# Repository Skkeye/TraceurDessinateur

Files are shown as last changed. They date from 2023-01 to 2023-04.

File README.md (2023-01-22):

# TraceurDessinateur
Projet Final Cegep

## Contexte/Origine
Le dessin est un art qui est difficile à apprendre et à maîtriser, alors l’option de prendre une photo pour décrire une scène devient très intéressante pour un artiste dépourvu de talent de dessinateur. Le TraceurDessinateur entre en jeu pour donner un compromis entre le dessin et la photo.

## Besoin General
Le besoin est de pouvoir dessiner un ou des objets sans pour autant avoir du talent pour dessiner. La partie cadrage et pinceau doivent être sans fil et rechargeable et doivent pouvoir être utilisés dans la majorité des environnements. La partie dessinateur doit être capable d'être configurable et facile à utiliser. 

## Objectif
L’objectif ici est de concevoir et de réaliser un pinceau 3d et une caméra de cadrage connectée par wifi au dessinateur qui lui pourra dessiner sur une feuille de papier.

## Fonctions Principales
La solution aura 3 parties principales en plus de la partie serveur qui connectera le tout. La première partie consiste d’une manette connectée au serveur par wifi, la deuxième d’une caméra qui détecte la position de la manette et la troisième d’un système de moteurs pas-à-pas pour dessiner sur une feuille de papier.
- La solution doit pouvoir voir et trouver la position de la manette via une caméra.
- La solution doit pouvoir choisir la couleur de la manette en fonction des couleurs perçus par la caméra.
- La solution doit pouvoir capter une force variable avec la manette.
- La solution doit consister d’une manette et d’une caméra portatives.
- La solution doit consister d’une manette et d’une caméra qui se connectent à un serveur WiFi dédié.
- La solution doit pouvoir dessiner à l'aide d’une machine CNC 2.5 axes.
- La solution doit être configurable via un menu contrôle avec un encodeur de rotation avec bouton.
- La solution doit avoir une caméra pour aider à positionner la caméra.
- La solution doit pouvoir être alimentée par une cellule LiPo pour la manette et la caméra.
- La solution doit avoir un bouton Marche/Arret sur le Dessinateur, la Caméra et la Manette.

## Contraintes
- Tension d’alimentation principale : 120 VAC
- Tension d’alimentation moteurs pas à pas : 4.1 VDC
- Tension d’alimentation de la caméra et la manette : 3.3v (LiPo 3.7v)
- Connexion sans fils : WiFi
- Application sur microcontrôleurs

## Livrables
- Produits Assembles : Manette, Camera, Dessinateur
- Logiciels installés sur les microcontrolleurs

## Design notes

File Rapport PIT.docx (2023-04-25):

Olivier David Laplante

Technique Systèmes Ordinés

Rapport du Projet d'Intégration en TSO TraceurDessinateur

Travail présenté à :

Francis Lance

Dans le cadre du cours

247-6E2-HU PIT

Groupe 201

Cégep de l’Outaouais

Campus Félix-Leclerc

Le 25 Avril 2023

# Table des matières

Table des matières 2

Introduction 3

But 3

Caractéristiques 3

Faisabilité 3

Dans le temps 3

Économiquement 3

Technologiquement 3

Diagrammes 5

Fonctionnel 5

Schématiques 6

Matriciel 8

Evaluation des coûts 9

Programmatique 10

Organigrammes 10

Manette 10

Serveur 11

Dessinateur 12

Pseudo-code 13

Manette 13

Serveur 14

Dessinateur 15

Code 16

Dessinateur.ino 16

StepperWrapper.h 22

StepperWrapper.cpp 26

Manette.ino 31

MQTTBroker.ino 38

Discussion 44

Problèmes et Solutions 44

Tests 44

Utilisations 44

Ameliorations 44

Reproduction 45

Matériel 45

Programmation 45

Environnement 45

Logiciels 45

Installer les pilotes 46

Procédé 46

Installer le logiciel du "Contrôleur USB" 46

Installer le logiciel du "Dessinateur" 46

Installer le logiciel de la "Manette" 46

Vérifications 46

Assemblage 47

Assurer le bon fonctionnement 47

Conclusion 48

Annexe A 49

Annexe B 50

Manuel de l’utilisateur 50

Consignes de sécurité 50

!Avertissements 50

!Attention 50

Attention 50

Table des matières 50

Caractéristiques 50

Définitions 50

Installation 51

Matérielle 51

Mise en marche 51

Mise en arrêt 51

Utilisation 51

Fonctionnement 51

Mode d'emploi 51

Dépannage 52

Section avancée 53

Prérequis 53

Accéder à la console de commandes 53

Les commandes 54

Réinstaller les logiciels 54

Installer les pilotes 54

Installer le logiciel du "Contrôleur USB" 54

Installer le logiciel du "Dessinateur" 55

Installer le logiciel de la "Manette" 55

Dépannage avancé 55

Annexe C 56

Manuel de dépannage 56

Problème 1 56

Tests 56

Hypothèses 56

Meilleurs Tests 56

Modifications 56

Vérification 56

Problème 2 56

Tests 56

Hypothèses 56

Meilleurs Tests 56

Modifications 56

Vérification 56

Problème 3 56

Tests 56

Hypothèses 56

Meilleurs Tests 56

Modifications 56

Vérification 56

# Introduction

## But

Le but était de concevoir et de réaliser un pinceau 3D connectée par wifi au dessinateur qui lui pourra dessiner sur une feuille de papier.

## Caractéristiques

## Faisabilité

### Dans le temps

Malgré que j'ai fini par manquer de temps pour achever le projet,

je le blâme purement sur la planification et sur les défis inutiles que je me suis placé pour rendre le projet plus intéressant. Si j'avais simplifié au lieu de complexifier et que mon échéancier était fondé sur mes capacités, je crois sincèrement que le temps n'aurait pas été un problème.

### Économiquement

À part la machine CNC qui m'a été prêté pour ce projet, toutes les autres composantes ne sont pas excessivement coûteuses (~100$ avec optimisations).

### Technologiquement

Les technologies utilisées dans ce projet sont très développées et accessibles pour tous. La composante la plus récente est le Raspberry Pi Pico W qui est sorti en juillet 2022.

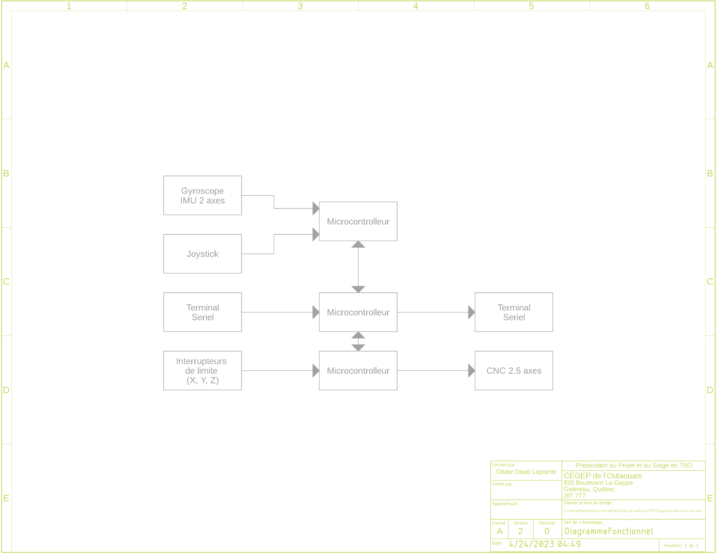
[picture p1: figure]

# Diagrammes

## Fonctionnel

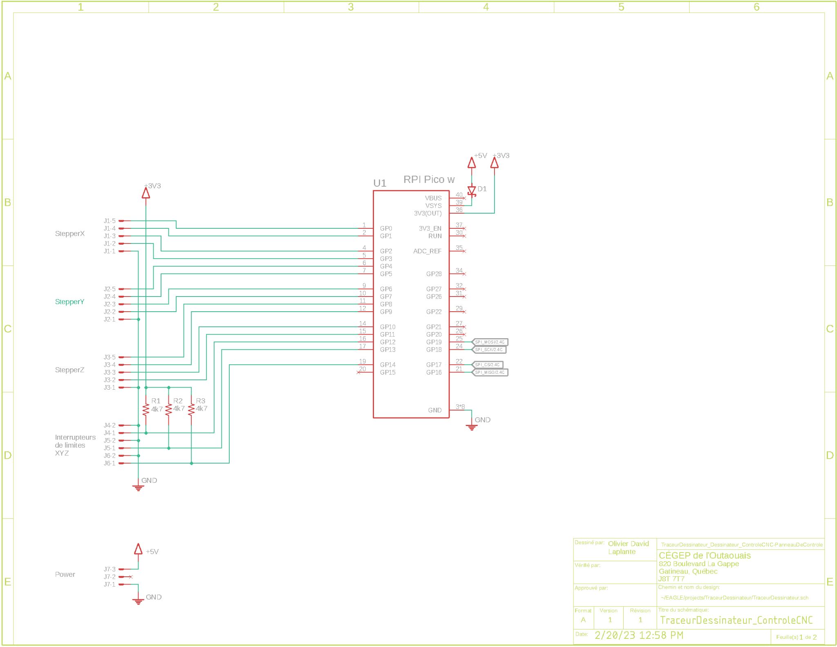
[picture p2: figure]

## Schématiques

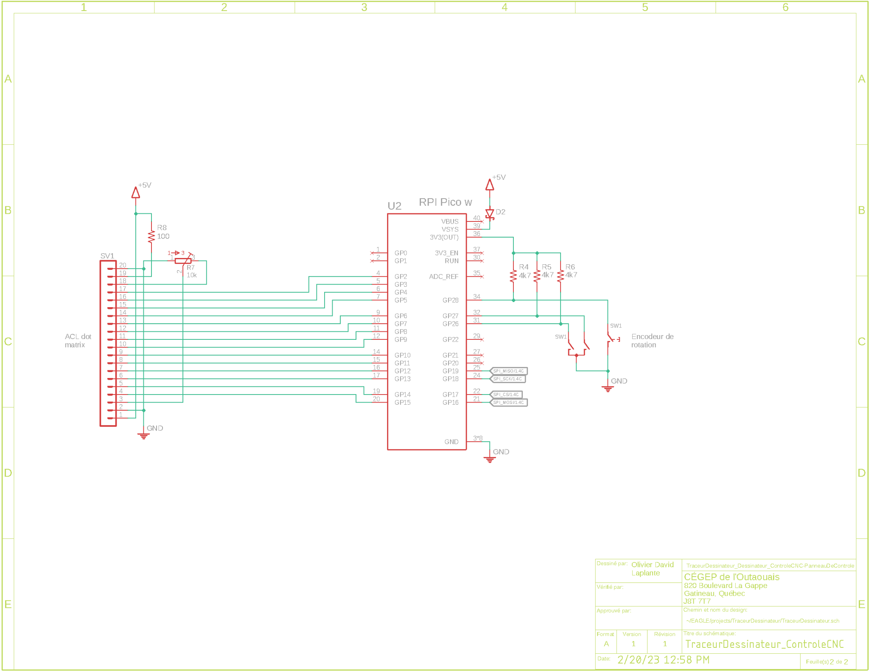
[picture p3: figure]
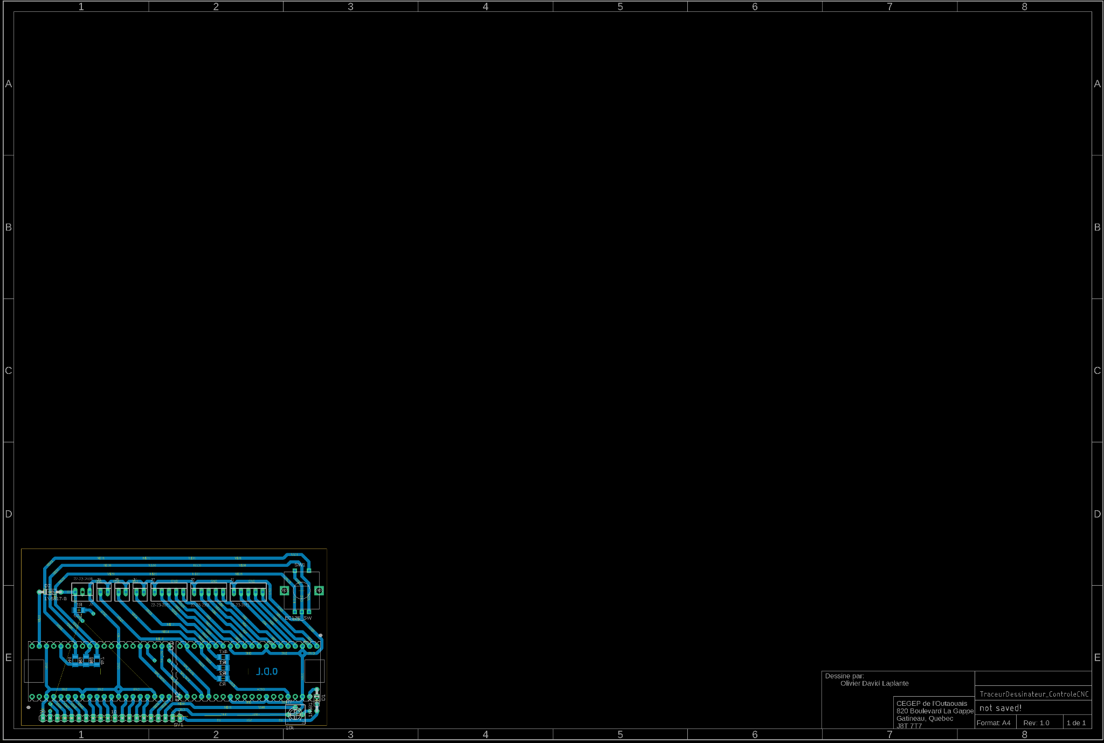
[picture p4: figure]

## Matriciel

## Evaluation des coûts

# Programmatique

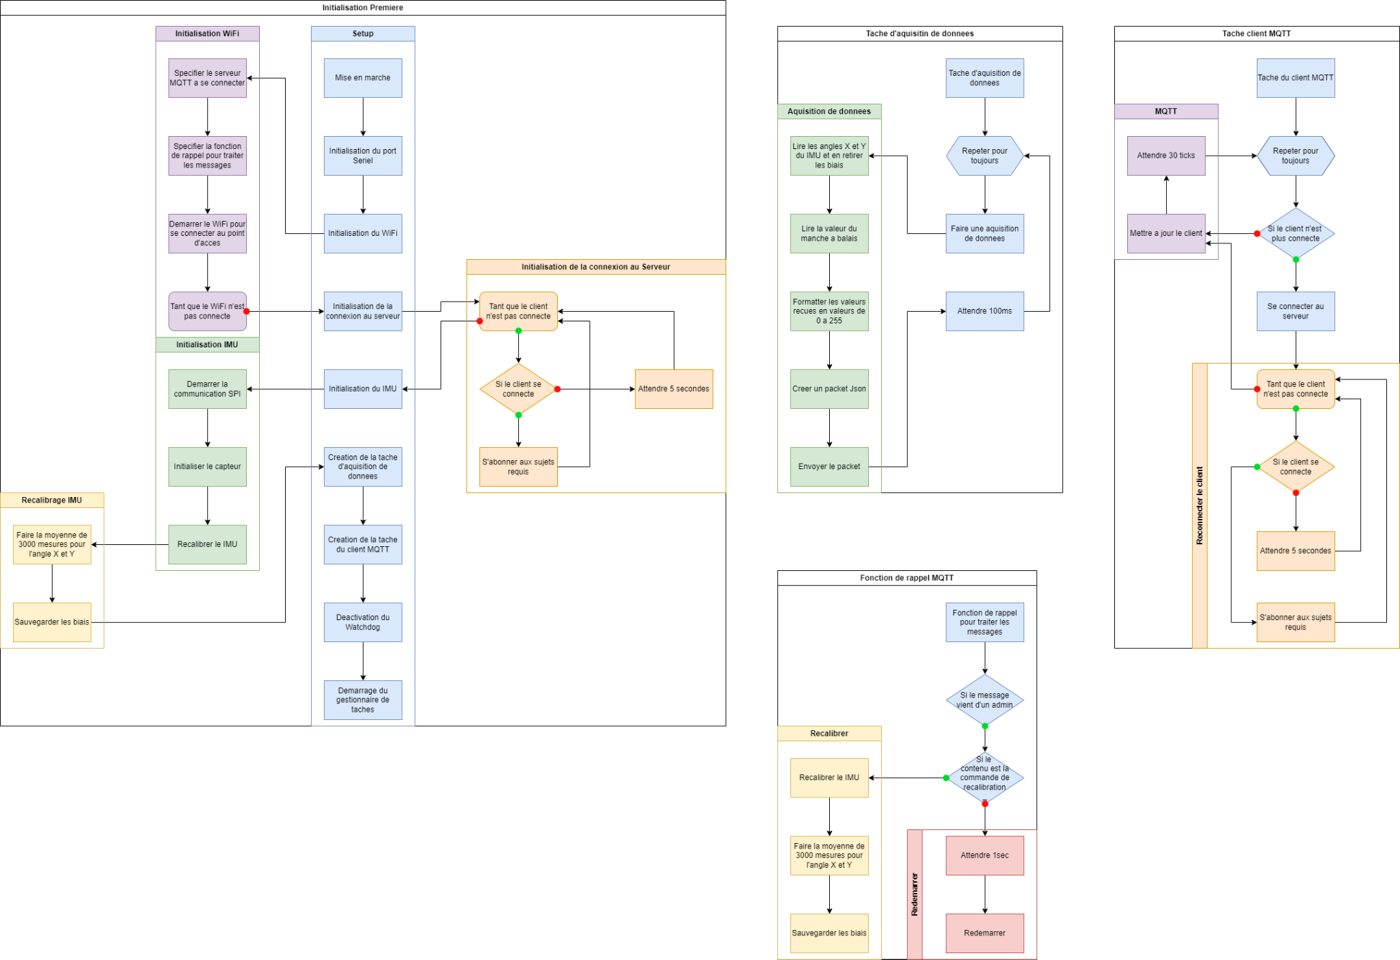
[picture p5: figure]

## Organigrammes

### Manette

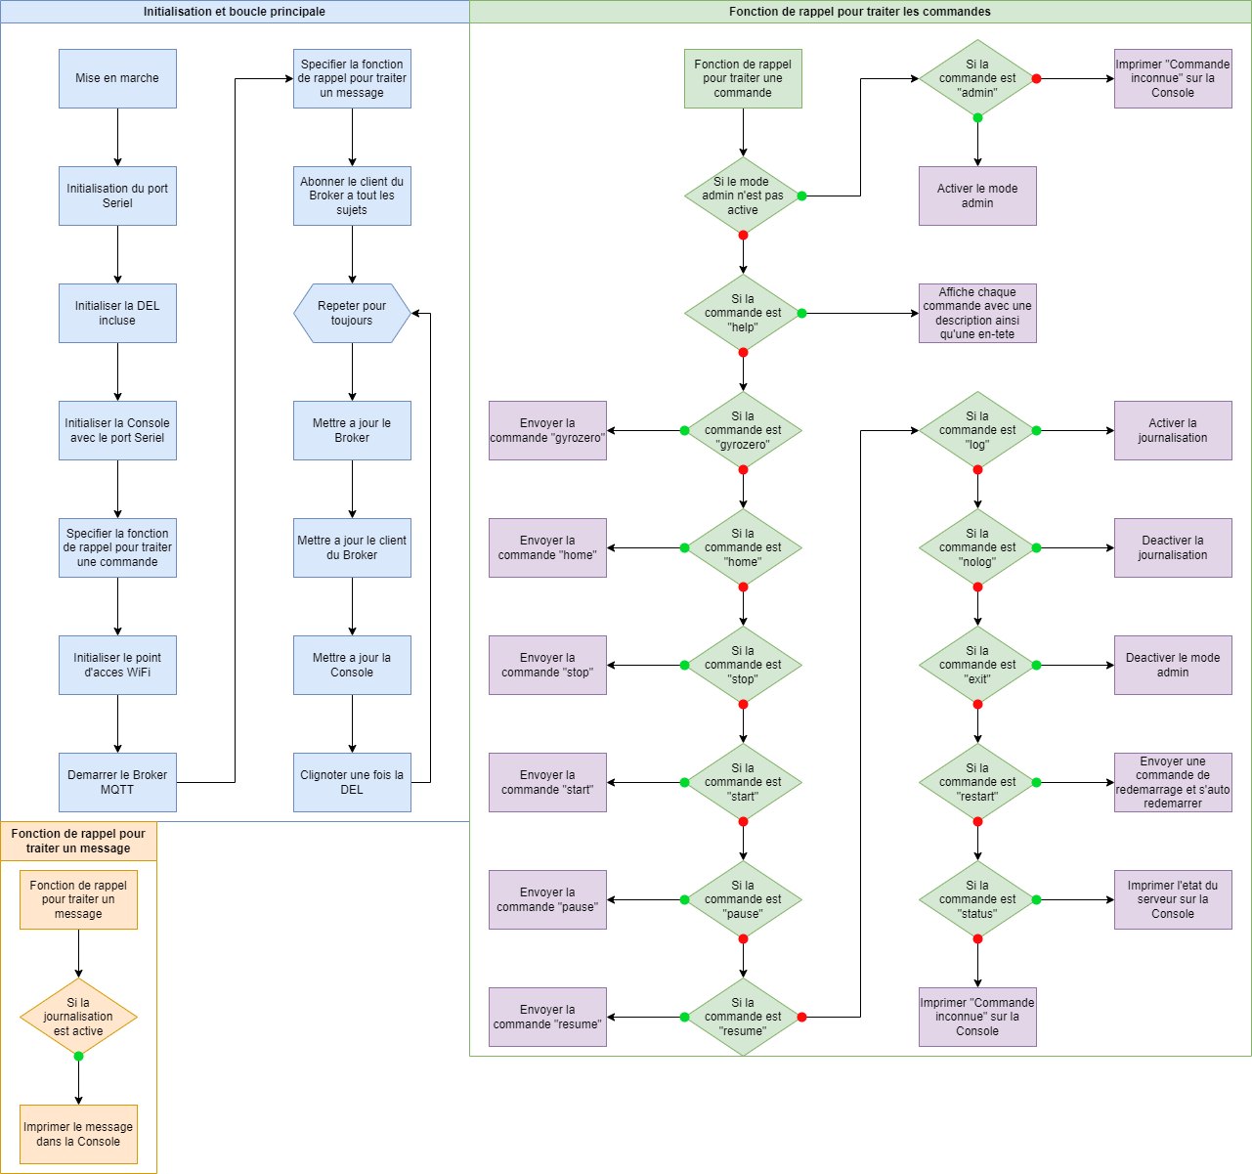
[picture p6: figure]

### Serveur

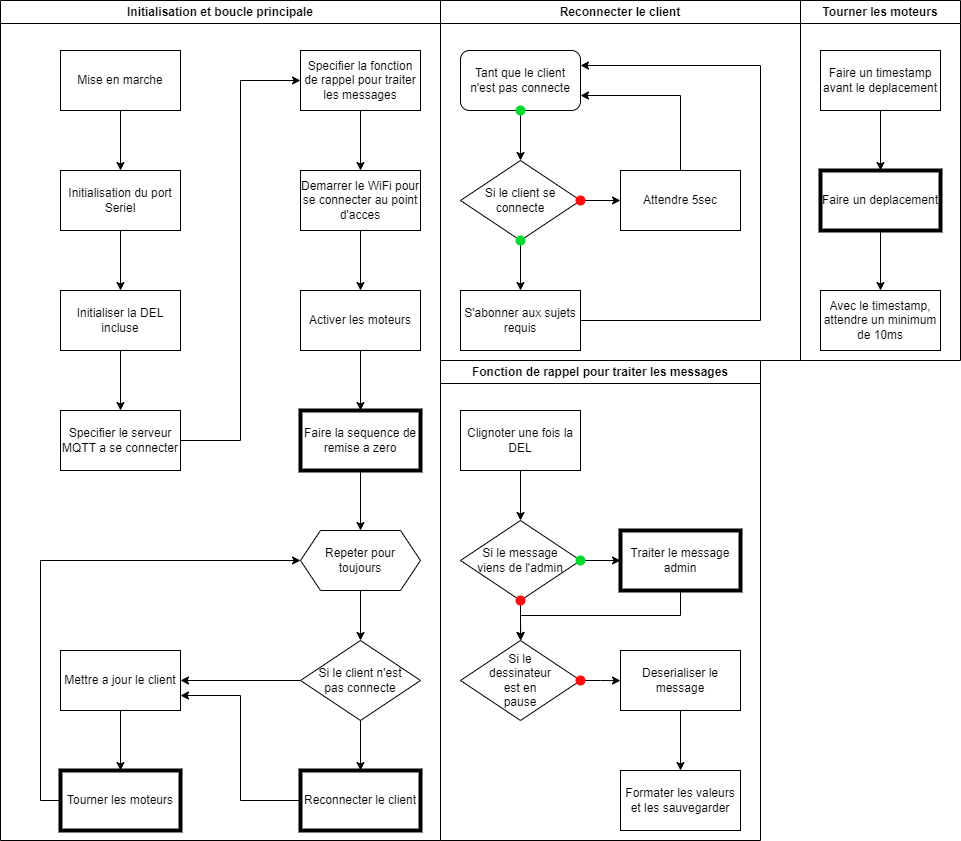
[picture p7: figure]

### Dessinateur

## Pseudo-code

### Manette

### Serveur

### Dessinateur

## Code

### Dessinateur.ino

/**

* @file AllInOneDessinateur.ino

* @brief Fichier principal du dessinateur

*

* Olivier David Laplante -- 8 Avril 2023 : Creation

*/

//#include <wiring_private.h>

#include "StepperWrapper.h"

#include <ArduinoJson.h>

#include <WiFi.h>

#include <PubSubClient.h>

// Definitions de constantes

#define NAME "Broker PIT"

#define PORT 1337

const IPAddress server_ip(192, 168, 144, 1);

// Variables et instances globales

DynamicJsonDocument doc(256);

char message[256] = "";

WiFiClient wifi_client;

PubSubClient client(wifi_client);

// Steppers

StepperWrapper stepper_x(0, 1, 2, 12, 12845 * 4);

StepperWrapper stepper_y(4, 5, 6, 13, 10752 * 4);

StepperWrapper stepper_z(8, 9, 10, 14, 1325 * 4, true);

ThreeAxisStepper steppers(&stepper_x, &stepper_y, &stepper_z);

bool paused = false;

// Variables pour les deltas

int deltaX = 0;

int deltaY = 0;

int deltaZ = 0;

/**

* @brief Fonction qui gère les messages admin

*

* @param topic : topic du message

* @param payload : payload du message

* @param lenght : longueur du payload

*/

void adminMessage(char *topic, uint8_t *payload, unsigned int lenght)

{

if (strcmp((char *)payload, "home") == 0) // home : mise a zero de la position

{

paused = true;

steppers.home();

paused = false;

}

else if (strcmp((char *)payload, "start") == 0) // start : demarrage des moteurs

{

steppers.enable();

}

else if (strcmp((char *)payload, "stop") == 0) // stop : arret des moteurs

{

steppers.disable();

}

else if (strcmp((char *)payload, "pause") == 0) // pause : pause les déplacements

{

paused = true;

}

else if (strcmp((char *)payload, "resume") == 0) // resume : reprend les deplacements

{

paused = false;

}

else if (strcmp((char *)payload, "restart") == 0) // restart : redémarre le RP2040

{

digitalWrite(LED_BUILTIN, HIGH);

delay(1000);

digitalWrite(LED_BUILTIN, LOW);

rp2040.reboot();

}

}

/**

* @brief Fonction qui fait clignoter la LED

*

*/

void vShortBlink()

{

digitalWrite(LED_BUILTIN, HIGH);

delay(1);

digitalWrite(LED_BUILTIN, LOW);

delay(1);

}

/**

* @brief Fonction qui gère les messages MQTT

*

* @param topic : topic du message

* @param payload : payload du message

* @param lenght : longueur du payload

*/

void callback(char *topic, uint8_t *payload, unsigned int lenght)

{

vShortBlink(); // blink led

// Si le message est un message admin

if (strcmp(topic, "admin") == 0)

{

adminMessage(topic, payload, lenght);

return;

}

if (paused) // Si le dessinateur est en pause on ne fait rien

{

return;

}

deserializeJson(doc, payload); // On désérialise le message

// On calcule les deltas

deltaY = (int)((short)doc["angle_x"] / 2) - 63;

deltaX = (int)((short)doc["angle_y"] / 2) - 63;

deltaZ = (int)((short)doc["bouton"] / 2) - 63;

client.flush();

}

/**

* @brief Fonction qui fait tourner les moteurs

*

*/

void runSteppers() {

unsigned long time = millis();

steppers.move(deltaX, deltaY, deltaZ);

delay((10 > (millis() - time)) ? (10 - (millis() - time)) : 0); // On attend jusqu'a 10ms pour avoir un delai constant

}

/**

* @brief Fonction qui reconnecte le client MQTT

*

*/

void reconnect()

{

// Boucle jusqu'à ce que le client se connecte

while (!client.connected())

{

Serial.print("Attempting MQTT connection...");

// essaye de se connecter

if (client.connect("arduinoClient"))

{

Serial.println("connected");

// Une fois connecté on s'abonne aux topics

client.subscribe("inTopic");

client.subscribe("admin");

}

else

{

Serial.print("failed, rc=");

Serial.print(client.state());

Serial.println(" try again in 5 seconds");

// On attend 5 secondes avant de recommencer

delay(5000);

}

}

}

/**

* @brief Fonction qui setup le dessinateur

*

*/

void setup()

{

Serial.begin(115200); // On initialise le port serie

pinMode(LED_BUILTIN, OUTPUT); // On initialise la LED builtin

// On initialise le client MQTT

client.setServer(server_ip, PORT);

client.setCallback(callback);

// On se connecte au WiFi

WiFi.mode(WIFI_STA);

WiFi.begin(NAME);

// on active les moteurs

steppers.enable();

// On met les moteurs a zero

steppers.home();

}

void loop()

{

if (!client.connected()) // Si le client n'est pas connecte on se reconnecte

{

reconnect();

}

client.loop(); // On fait tourner le client MQTT

runSteppers(); // On fait tourner les moteurs

}

### StepperWrapper.h

/**

* @file StepperWrapper.h

* @brief Les definitions pour manipuler des moteurs steppers

*

* Olivier David Laplante -- 8 Avril 2023 : Creation

*/

#pragma once

/**

* @class StepperWrapper

* @brief Objet pour simplifier un moteur stepper

*

*/

class StepperWrapper {

private:

int dir_pin, step_pin, en_pin, home_pin;

long max_distance_from_origin;

bool positive_direction;

bool direction;

/**

* @brief Initialise les pins relative au moteur

*/

void initPins();

public:

long distance_from_origin;

/**

* @brief Le constructeur pour le stepper

*

* @param dir La pin de direction

* @param step La pin de step

* @param en La pin enable

* @param home La pin de l'interrupteur de limite

* @param max_distance La distance maximale en pas

* @param flip_dir Change la direction par defaut (defaut = false)

*/

StepperWrapper(int dir, int step, int en, int home, int max_distance,

bool flip_dir = false);

/**

* @brief Fait un pas

*

* @param force Force le pas meme si on est a la limite

*/

void step(bool force);

/**

* @brief Change l'etat de la pin de direction

*

* @param dir La nouvelle direction

*/

void setDir(bool dir);

/**

* @brief Change l'etat de la pin enable

*

* @param en L'etat

*/

void setEnabled(bool en);

/**

* @brief Verifie si l'interrupteur est enfonce

*

* @return bool Si enfonce

*/

bool isHome();

};

/**

* @class ThreeAxisStepper

* @brief Manipule 3 moteurs stepper simultanement

*

*/

class ThreeAxisStepper {

private:

StepperWrapper *stepper_x, *stepper_y, *stepper_z;

/**

* @brief Utilise pour repartir egalement les pas des moteurs

*

* @param this_step Le nombre de pas que le moteur a fait durant ce

* deplacement

* @param count Le nombre de pas de ce deplacement

* @param steps_moving Le nombre de pas requis pour ce moteur pour ce

* deplacement

* @param largest_step_count Le plus grand nombre de pas requis pour de

* deplacement

* @return Si le moteur fait un pas

*/

bool doesStep(int this_step, int count, int steps_moving,

int largest_step_count);

public:

/**

* @brief Le constructeur

*

* @param stepperX Pointeur vers le StepperWrapper du moteur de l'axe X

* @param stepperY Pointeur vers le StepperWrapper du moteur de l'axe Y

* @param stepperZ Pointeur vers le StepperWrapper du moteur de l'axe Z

*/

ThreeAxisStepper(StepperWrapper *stepperX, StepperWrapper *stepperY,

StepperWrapper *stepperZ);

/**

* @brief Execute un deplacement

*

* @param deltaX Le nombre de pas pour l'axe X

* @param deltaY Le nombre de pas pour l'axe Y

* @param deltaZ Le nombre de pas pour l'axe Z

*/

void move(int deltaX, int deltaY, int deltaZ);

/**

* @brief Remet a 0 les moteurs

*/

void home();

/**

* @brief Fonctions pour activer et desactiver les moteurs

*/

void disable();

void enable();

};

### StepperWrapper.cpp

/**

* @file StepperWrapper.cpp

* @brief Le code pour manipuler des moteurs steppers

*

* Olivier David Laplante -- 8 Avril 2023 : Creation

*/

#include "StepperWrapper.h"

#include <Arduino.h>

void StepperWrapper::initPins() {

pinMode(this->dir_pin, OUTPUT);

pinMode(this->step_pin, OUTPUT);

pinMode(this->en_pin, OUTPUT);

pinMode(this->home_pin, INPUT);

digitalWrite(this->dir_pin, LOW);

digitalWrite(this->step_pin, LOW);

digitalWrite(this->en_pin, HIGH); // HIGH = disabled

}

StepperWrapper::StepperWrapper(int dir, int step, int en, int home,

int max_distance, bool flip_dir) {

this->dir_pin = dir;

this->step_pin = step;

this->en_pin = en;

this->home_pin = home;

this->distance_from_origin = 0;

this->max_distance_from_origin = max_distance;

this->positive_direction = !flip_dir;

this->direction = false;

this->initPins();

}

void StepperWrapper::step(bool force = false) {

// check if we are at the limit

// if (this->distance_from_origin >= this->max_distance_from_origin && !force) {

// if (this->direction == this->positive_direction) {

// delayMicroseconds(50);

// return;

// }

// } else if (this->distance_from_origin <= 0 && !force) {

// if (this->direction != this->positive_direction) {

// delayMicroseconds(50);

// return;

// }

// }

// // keep track of distance from origin

// if (this->direction) {

// this->distance_from_origin++;

// } else {

// this->distance_from_origin--;

// }

digitalWrite(this->step_pin, HIGH);

delayMicroseconds(25);

digitalWrite(this->step_pin, LOW);

delayMicroseconds(25);

}

void StepperWrapper::setDir(bool dir) {

this->direction = dir;

digitalWrite(this->dir_pin, this->positive_direction == dir);

}

void StepperWrapper::setEnabled(bool en) {

digitalWrite(this->en_pin, !en);

}

bool StepperWrapper::isHome() {

return digitalRead(this->home_pin);

}

ThreeAxisStepper::ThreeAxisStepper(StepperWrapper *stepperX,

StepperWrapper *stepperY,

StepperWrapper *stepperZ) {

this->stepper_x = stepperX;

this->stepper_y = stepperY;

this->stepper_z = stepperZ;

}

bool ThreeAxisStepper::doesStep(int this_step, int count, int steps, int largest_step_count) {

int num = (int)ceilf(count * (float)((float)largest_step_count / (float)(steps + 1)));

return (num == this_step && count <= steps);

}

void ThreeAxisStepper::move(int deltaX, int deltaY, int deltaZ) {

// On met les directions des moteurs

(*this->stepper_x).setDir(deltaX >= 0);

(*this->stepper_y).setDir(deltaY >= 0);

(*this->stepper_z).setDir(deltaZ >= 0);

// Attendre pour que les moteurs soient prêts

delayMicroseconds(10);

// Normaliser les pas

deltaX *= (deltaX < 0) ? -1 : 1;

deltaY *= (deltaY < 0) ? -1 : 1;

deltaZ *= (deltaZ < 0) ? -1 : 1;

// Trouver le plus grand nombre de pas à faire

int largest_step_count = (deltaX > deltaY) ? deltaX : deltaY;

largest_step_count = (largest_step_count > deltaZ) ? largest_step_count : deltaZ;

// Initialiser les compteurs de pas pour chaque moteur

int count_x = 1, count_y = 1, count_z = 1;

// Faire les pas un à un

for (int this_step = 1; this_step < largest_step_count + 1; this_step++) {

if (doesStep(this_step, count_x, deltaX, largest_step_count)) { // Si on doit faire un pas pour ce moteur

(*this->stepper_x).step(); // Faire le pas

count_x++; // Incrémenter le compteur de pas pour ce moteur (pour savoir quand on doit faire un pas)

} else { // Sinon, attendre pour compenser les pas manqués

delayMicroseconds(50);

}

if (doesStep(this_step, count_y, deltaY, largest_step_count)) { // Si on doit faire un pas pour ce moteur

(*this->stepper_y).step(); // Faire le pas

count_y++; // Incrémenter le compteur de pas pour ce moteur (pour savoir quand on doit faire un pas)

} else { // Sinon, attendre pour compenser les pas manqués

delayMicroseconds(50);

}

if (doesStep(this_step, count_z, deltaZ, largest_step_count)) { // Si on doit faire un pas pour ce moteur

(*this->stepper_z).step(); // Faire le pas

count_z++; // Incrémenter le compteur de pas pour ce moteur (pour savoir quand on doit faire un pas)

} else { // Sinon, attendre pour compenser les pas manqués

delayMicroseconds(50);

}

}

}

void ThreeAxisStepper::home() {

// un moteur à la fois

while (!(*this->stepper_x).isHome()) {

(*this->stepper_x).setDir(true);

(*this->stepper_x).step(true);

delayMicroseconds(90);

}

while (!(*this->stepper_y).isHome()) {

(*this->stepper_y).setDir(false);

(*this->stepper_y).step(true);

delayMicroseconds(90);

}

while (!(*this->stepper_z).isHome()) {

(*this->stepper_z).setDir(false);

(*this->stepper_z).step(true);

delayMicroseconds(90);

}

// remettre les distances à 0

(*this->stepper_x).distance_from_origin = 0;

(*this->stepper_y).distance_from_origin = 0;

(*this->stepper_z).distance_from_origin = 0;

}

void ThreeAxisStepper::disable() {

(*this->stepper_x).setEnabled(false);

(*this->stepper_y).setEnabled(false);

(*this->stepper_z).setEnabled(false);

}

void ThreeAxisStepper::enable() {

(*this->stepper_x).setEnabled(true);

(*this->stepper_y).setEnabled(true);

(*this->stepper_z).setEnabled(true);

}

### Manette.ino

/**

* @file Manette.ino

* @brief Code Manette

*

* Olivier David Laplante - 11 Avril 2023 - Creation

*/

#include <ArduinoJson.h>

#include <PubSubClient.h>

#include <MPU6050_tockn.h>

#include <WiFi.h>

#include <Wire.h>

#include <freertos/FreeRTOS.h>

#include <freertos/task.h>

#include <esp_task_wdt.h>

// Configurations WiFi/Serveur/Capteurs

#define SSID "Broker PIT"

#define ADDR "192.168.144.1"

#define PORT 1337

#define PIN_BUTTON 37

// Instantiation du Capteur/ClientWiFi/JSON

MPU6050 xManetteIMU(Wire);

WiFiClient wifi_client;

PubSubClient client(wifi_client);

DynamicJsonDocument doc(256);

char message[256] = "";

// Biais du IMU

float fOffsetX;

float fOffsetY;

/**

* @brief Assure la connexion WiFi et Serveur

*/

void assertConnection()

{

while (WiFi.status() != WL_CONNECTED)

{

Serial.print('.');

delay(500);

}

while (!client.connected()) {

connectToServer();

};

}

/**

* @brief Initialise la connexion au reseau WiFi

*/

void initWiFi()

{

Serial.println("Connexion au controlleur...");

client.setServer(ADDR, PORT);

client.setCallback(callback);

WiFi.mode(WIFI_STA);

WiFi.begin(SSID);

while (WiFi.status() != WL_CONNECTED)

{

Serial.print('.');

delay(500);

}

Serial.println("OK");

Serial.println();

}

/**

* @brief Initialise la connexion au Serveur

*/

void connectToServer()

{

Serial.println("Connexion au serveur...");

while (!client.connected()) {

Serial.print("Attempting MQTT connection...");

if (client.connect("arduinoClient")) {

Serial.println("connected");

client.subscribe("outTopic");

client.subscribe("admin");

} else {

Serial.print("failed, rc=");

Serial.print(client.state());

Serial.println(" try again in 5 seconds");

delay(5000);

}

}

Serial.println("OK");

}

/**

* @brief Calcule les biais du IMU

*/

void recalibrateIMU()

{

float fCumulX = 0;

float fCumulY = 0;

for(int i = 0; i < 3000; i++) {

xManetteIMU.update();

fCumulX += xManetteIMU.getAccAngleX();

fCumulY += xManetteIMU.getAccAngleY();

}

fOffsetX = fCumulX / 3000;

fOffsetY = fCumulY / 3000;

}

/**

* @brief Initialise le IMU

*/

void initIMU()

{

Wire.begin();

xManetteIMU.begin();

recalibrateIMU();

}

/**

* @brief Met a jour les donnees du IMU et du bouton

*/

void updateDataIMU()

{

xManetteIMU.update();

float fAngleX = xManetteIMU.getAccAngleX() - fOffsetX;

float fAngleY = xManetteIMU.getAccAngleY() - fOffsetY;

int iButtonValue = analogRead(PIN_BUTTON);

// Serial.println(round(fAngleX));

// Serial.println(round(fAngleY));

// Serial.println(iButtonValue);

/**

* @brief Formatte les donnees brutes en un nombre (short) de 0-255

*/

short sAngleX = ((128 + round(fAngleX * 2)) > 255) ? 255 : ((128 + round(fAngleX * 2)) < 0) ? 0 : (128 + round(fAngleX * 2));

short sAngleY = ((128 + round(fAngleY * 2)) > 255) ? 255 : ((128 + round(fAngleY * 2)) < 0) ? 0 : (128 + round(fAngleY * 2));

short sButtonValue = floor(iButtonValue / 16);

// Serial.println(sAngleX);

// Serial.println(sAngleY);

// Serial.println(sButtonValue);

doc["angle_x"] = sAngleX;

doc["angle_y"] = sAngleY;

doc["bouton"] = sButtonValue;

serializeJson(doc, message, 256);

client.publish("inTopic", message);

client.flush();

}

/**

* @brief Callback pour le recalibrage du IMU sur un message MQTT admin

*/

void callback(char *topic, uint8_t *payload, unsigned int lenght)

{

// "admin" -> "recalibrate" -> recalibrateIMU()

if (strcmp(topic, "admin") == 0)

{

if (strcmp((char *)payload, "gyrozero") == 0)

{

recalibrateIMU();

Serial.println("Recalibration du IMU");

} else if (strcmp((char *)payload, "restart") == 0) {

delay(1000);

esp_restart();

}

}

}

/**

* @brief Appelle les fonctions d'initialisation et demarre les taches

*/

void setup()

{

Serial.begin(115200);

initWiFi();

connectToServer();

initIMU();

xTaskCreatePinnedToCore(vDataTask, "vDataTask", 10000, NULL, 2, NULL, 1);

xTaskCreatePinnedToCore(vMQTTTask, "vMQTTTask", 10000, NULL, 1, NULL, 1);

esp_task_wdt_delete(NULL);

esp_task_wdt_deinit();

}

/**

* @brief Appelle les fonctions de mise a jour du IMU et du bouton

*/

void vDataTask(void *pvParameters)

{

while (1)

{

updateDataIMU();

vTaskDelay(pdMS_TO_TICKS(100));

}

}

/**

* @brief Appelle les fonctions de connexion au serveur

*/

void vMQTTTask(void *pvParameters)

{

while (1)

{

if (!client.connected())

{

connectToServer();

}

client.loop();

vTaskDelay(30);

}

}

void loop() {

}

### MQTTBroker.ino

/**

* @file MQTTBroker.ino

* @brief Programme principal du broker MQTT (Serveur)

*

* Olivier David Laplante - 20 Avril 2023 - Creation

*/

// Fichiers d'inclusion

#include <WiFi.h>

#include <TinyMqtt.h>

#include <TinyConsole.h>

#include <ArduinoJson.h>

// configurations du broker

#define SSID "Broker PIT"

#define PORT 1337

#define RETAIN 10

IPAddress server_ip(192, 168, 144, 11);

IPAddress gateway(192, 168, 144, 1);

IPAddress subnet(255, 255, 255, 0);

// broker et client

MqttBroker broker(PORT);

MqttClient adminClient(&broker);

// TinyConsole Console;

// variables pour le mode admin

bool bAdminLogging = false;

bool bAdminActive = false;

/**

* @brief Fonction qui affiche le logo du projet

*/

void printBanner() {

// "TraceurDessinateur" en art ASCII

Console << " ______ " << endl;

Console << "(_) | " << endl;

Console << " | ,_ __, __ _ ,_ " << endl;

Console << " _ |/ | / | / |/ | | / | " << endl;

Console << " (_/ |_/\\_/|_/\\___/|__/ \\_/|_/ |_/ " << endl;

Console << endl;

Console << " ____ " << endl;

Console << " (| \\ o " << endl;

Console << " | | _ , , _ _ __, _|_ _ ,_ " << endl;

Console << " _| ||/ / \\_/ \\_| / |/ | / | | |/ | | / | " << endl;

Console << "(/\\___/ |__/ \\/ \\/ |_/ | |_/\\_/|_/|_/|__/ \\_/|_/ |_/" << endl;

Console << endl;

}

/**

* @brief Gere les commandes de l'admin

*

* @param command le texte de la commande

*/

void consoleCallback(const std::string &command) {

if (!bAdminActive) { // Si le mode admin n'est pas active

if (command == "admin") { // Si la commande est "admin"

bAdminActive = true; // Active le mode admin

Console << "Mode admin active" << endl;

} else {

Console << "Commande inconnue" << endl;

}

Console.prompt();

return;

}

// Si le mode admin est active

if (command == "help") { // affiche l'aide

Console << endl << endl << endl;

printBanner();

Console << endl << endl;

Console << "Commandes:" << endl;

Console << "help: affiche l'aide" << endl;

Console << "log: affiche les messages du broker" << endl;

Console << "nolog: ne plus afficher les messages du broker" << endl;

Console << "gyrozero: recalibre la manette" << endl;

Console << "home: met a zero le dessinateur et le recentre" << endl;

Console << "stop: arrete le dessinateur" << endl;

Console << "start: demarre le dessinateur" << endl;

Console << "pause: met en pause le dessinateur" << endl;

Console << "resume: reprend le dessinateur" << endl;

Console << "restart: redemarre le serveur" << endl;

Console << "admin: entre dans le mode admin" << endl;

Console << "status: affiche le status des connexions" << endl;

Console << "exit: quitte le mode admin" << endl;

} else if (command == "gyrozero") { // recalibre la manette

adminClient.publish("admin", "gyrozero", RETAIN);

} else if (command == "home") { // recentre le dessinateur

adminClient.publish("admin", "home", RETAIN);

} else if (command == "stop") { // arrete le dessinateur

adminClient.publish("admin", "stop", RETAIN);

} else if (command == "start") { // demarre le dessinateur

adminClient.publish("admin", "start", RETAIN);

} else if (command == "pause") { // met en pause le dessinateur

adminClient.publish("admin", "pause", RETAIN);

} else if (command == "resume") { // reprend le dessinateur

adminClient.publish("admin", "resume", RETAIN);

} else if (command == "log") { // affiche les messages du broker

bAdminLogging = true;

} else if (command == "nolog") { // ne plus afficher les messages du broker

bAdminLogging = false;

} else if (command == "exit") { // quitte le mode admin

bAdminActive = false;

Console << "Mode admin desactive" << endl;

} else if (command == "restart") { // redemarre le serveur

adminClient.publish("admin", "restart", RETAIN);

delay(1000);

rp2040.reboot();

} else if (command == "status") { // affiche le status des connexions

Console << "Status des connexions:" << endl;

Console << " - Admin: " << (bAdminActive ? "active" : "desactive") << endl;

Console << " - Logging: " << (bAdminLogging ? "active" : "desactive") << endl;

Console << " - Clients: " << broker.clientsCount() << endl;

} else { // commande inconnue

Console << "Commande inconnue" << endl;

}

}

/**

* @brief Callback appele lorsqu'un message est recu

*

* @param client le client qui a recu le message

* @param topic le topic sur lequel le message a ete recu

* @param payload le message recu

* @param lenght la taille du message

*/

void logCallback(const MqttClient *client, const Topic &topic, const char *payload, unsigned int lenght) {

if (bAdminLogging == true) {

Console << topic.str() << ": " << payload << endl;

}

}

/**

* @brief Fonction d'initialisation

*/

void setup() {

Serial.begin(115200);

pinMode(LED_BUILTIN, OUTPUT);

Console.begin(Serial);

Console.setCallback(consoleCallback);

printBanner();

Console << endl << endl << endl;

Console << "MQTT Broker PIT" << endl << endl;

WiFi.mode(WIFI_AP);

WiFi.softAPConfig(server_ip, gateway, subnet);

WiFi.softAP(SSID);

Console << "Point d'acces WiFi configure" << endl;

Console << "SSID: " << SSID << endl;

Console << "IP: " << server_ip.toString() << ":" << PORT << endl;

Console << "Gateway: " << gateway.toString() << endl;

Console << "Subnet mask: " << subnet.toString() << endl << endl;

// init du broker

broker.begin();

Console << "Broker initialise" << endl << endl;

// init du Callback du client admin

adminClient.setCallback(logCallback);

adminClient.subscribe("inTopic");

adminClient.subscribe("outTopic");

adminClient.subscribe("admin");

}

void loop() {

broker.loop();

adminClient.loop();

Console.loop();

// blink tres court

digitalWrite(LED_BUILTIN, HIGH);

delay(1);

digitalWrite(LED_BUILTIN, LOW);

delay(1);

}

# Discussion

## Problèmes et Solutions

## Tests

## Utilisations

## Ameliorations

# Reproduction

## Matériel

- Raspberry Pi Pico W (x2)

- Esp32 Pico Kit

- Joystick

- MPU-6050 GY-521

- Li-ion

- Chargeur Li-ion

- CNC 2.5 axes

- PSU d'ordinateur 12v/5v/3v3

- Connecteur 1x6 femelle (x3)

- Connecteur 1x2 femelle (x3)

- Connecteur 1x3 femelle

- Connecteur 1x20 femelle (x2)

- Breadboard medium (x2)

- Câble micro USB

- Schottky 1N5817

- Résistance 4k7 (x3)

## Programmation

### Environnement

#### Logiciels

- Visual Studio Code (+ extension Arduino) (aka VSCode)

- Arduino IDE

- Git

- GitFiend (optionnel)

- Python

- Putty

- EagleCAD

- InstalleurTD (https://github.com/Skkeye/TraceurDessinateur/releases/download/v0.1.0-alpha/InstalleurTD.zip)

- Pilotes WinUSB

- Scripts d'installation

- 7zip (https://www.7-zip.org)

- Pilotes CP210x (https://www.silabs.com/documents/public/software/CP210x_Universal_Windows_Driver.zip)

- PuTTY (https://the.earth.li/~sgtatham/putty/latest/w64/putty-64bit-0.78-installer.msi)

#### Installer les pilotes

1. WinUSB avec Zadig (un pico doit etre connecte durant l'installation)

2. CP210x

### Procédé

1. Avant tout, installer les logiciels ci-dessus

2. Avec Git/GitFiend, faites un clone de mon Git repo : https://github.com/Skkeye/TraceurDessinateur.git

cmd>`git clone https://github.com/Skkeye/TraceurDessinateur.git`

3. Ouvrez le dossier avec VSCode

4. Naviguez dans `Code/Test/Sanity/`

5. Utilisez l'extension Arduino pour configurer l'environnement `Ctrl+Shift+p` `Arduino: Initialize`

- S'il y a une erreur, utilisez Arduino IDE pour comme environnement de programmation

6. Procédés de programmation :

___

#### Installer le logiciel du "Contrôleur USB"

1. Prendre le "Contrôleur USB" et le brancher dans l'ordinateur en gardant le bouton blanc appuyé

2. Exécutez "Installer_Controleur.bat" et attendre que la fenêtre se referme

3. Retirez le "Contrôleur USB" de l'ordinateur

#### Installer le logiciel du "Dessinateur"

1. Prendre le "Dessinateur" et le brancher dans l'ordinateur en gardant le bouton blanc appuyé

2. Exécutez "Installer_Dessinateur.bat" et attendre que la fenêtre se referme

3. Retirez le "Dessinateur" de l'ordinateur

#### Installer le logiciel de la "Manette"

1. Prendre la "Manette" et le brancher dans l'ordinateur en gardant le bouton étiqueté "Boot" appuyé

2. Exécutez "Installer_Manette.bat", vous pouvez relâcher le bouton une fois connecte

3. Une fois la fenêtre refermée, vous pouvez retirer la "Manette" de l'ordinateur

___

## Vérifications

- Matériel

- Logiciel

## Assemblage

- Utilisez EAGLE pour générer les fichiers gerber depuis les fichiers brd

- Commandez les circuits imprimés avec les gerbers générés à la dernière étape

- Faire ces connections:

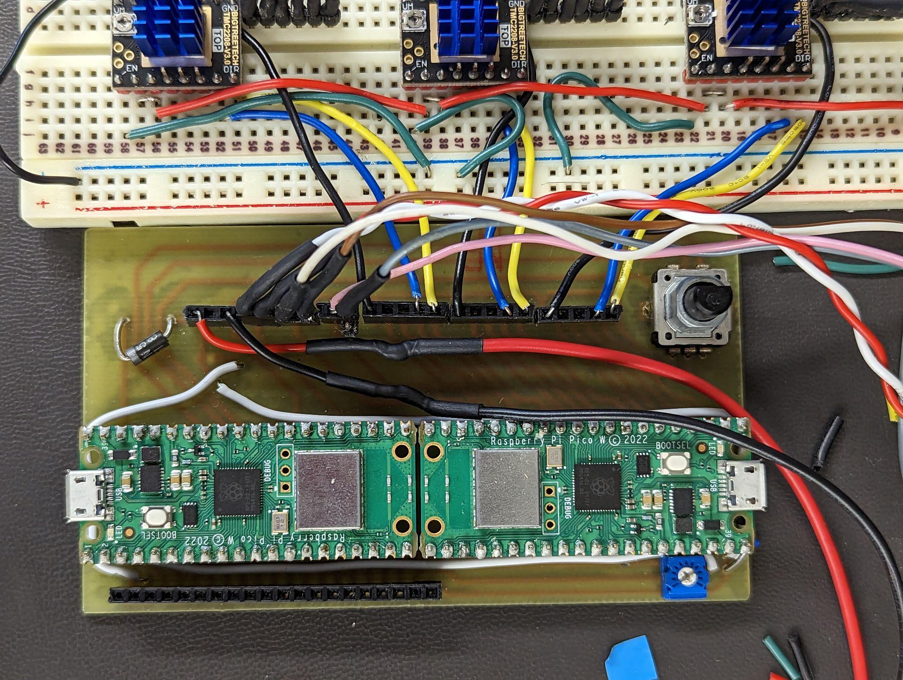
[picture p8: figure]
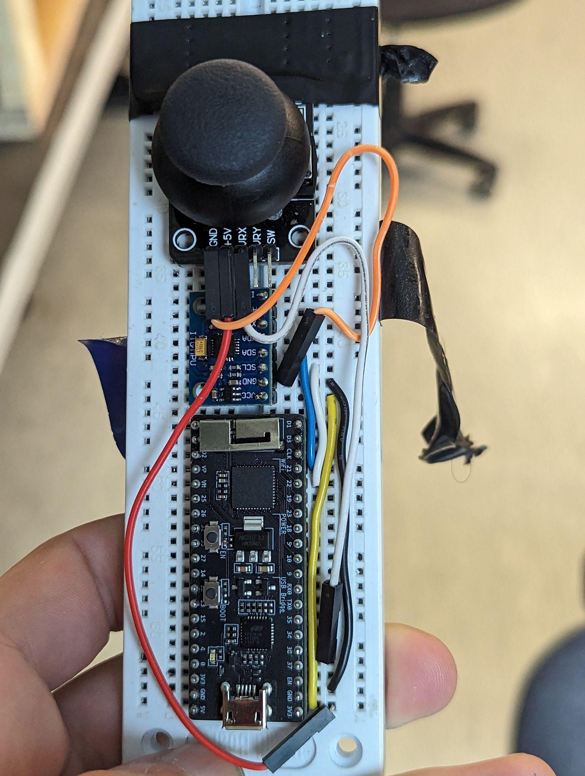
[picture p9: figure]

## Assurer le bon fonctionnement

- Lorsque le Dessinateur s'allume, il devrait se remettre à zéro

- Lorsque la DEL sur le Dessinateur fait une impulsion, cela signifie qu'il a reçu un message MQTT.

# Conclusion

# Annexe A

AllInOneDessinateur.ino : Code principal du dessinateur

StepperWrapper.h : Fichier d’inclusion du module de contrôle des steppers

StepperWrapper.cpp : Code du module de contrôle des steppers

…

# Annexe B

## Manuel de l’utilisateur

## Consignes de sécurité

### !Avertissements

- Ne pas ouvrir le bloc d'alimentation

### !Attention

- Ne pas être trop proche du "Dessinateur" lorsqu'il est en fonction
- Ne pas plier, couper, percer ou mettre un stress sur la batterie Lithium
- Ne pas déplacer manuellement la tête du "Dessinateur"

### Attention

- Ne pas laisser le "Dessinateur" en fonction pour une durée de plus de 2 heures

## Table des matières

## Caractéristiques

- Peut dessiner sur tout matériau qui n'a pas plus de 3 cm d'épaisseur et qui est compatible avec le crayon choisi
- Peut être contrôlé sur une distance de 0 à 20 mètres du "Contrôleur USB"

## Définitions

- Le "Dessinateur"
- Le "Câble d'alimentation"
- La "Manette"
- Le "Contrôleur USB"

## Installation

### Matérielle

- Connectez le "Câble d'alimentation" dans la prise d'alimentation du "Dessinateur"
- Branchez le "Câble d'alimentation" dans une prise murale

### Mise en marche

- Branchez le "Contrôleur USB" dans une prise USB alimentée
- Allumez le "Dessinateur" avec l'interrupteur située proche de la prise d'alimentation
- Connectez la batterie à la "Manette"

### Mise en arrêt

- Déactivez l'interrupteur situé proche de la prise d'alimentation du "Dessinateur"
- Déconnectez la batterie de la "Manette"
- Débranchez le "Contrôleur USB"

## Utilisation

### Fonctionnement

Une fois le "Dessinateur" calibre, l'inclinaison de la "Manette" déplacera le crayon de gauche à droite et de proche a loin. Tirer ou pousser sur le joystick de la "Manette" descendera et remontera le crayon.

### Mode d'emploi

- Gardez la "Manette" à l'horizontale pour ne pas changer la position de la tête du "Dessinateur"
- Inclinez la "Manette" dans une direction pour contrôler la position de la tête du "Dessinateur"
- Poussez le joystick de la "Manette" pour abaisser le crayon sur la surface à dessiner
- Tirez le manche à balai de la "Manette" pour remonter le crayon
- En cas d'urgence, débranchez immédiatement le "Câble d'alimentation" de la prise murale et ensuite éteindre l'interrupteur du "Dessinateur" située proche de la prise d'alimentation

## Dépannage

- Si la "Manette" ne contrôle toujours pas le "Dessinateur" :
  - Éteindre tout
  - Branchez le "Controlleur USB" en premier
  - Ensuite, allumez le "Dessinateur"
  - Et finalement, allumez la "Manette"
  - Sinon se référer au Dépannage de la section avancée
- S'il y a un délai trop important :
  - Éteindre la "Manette"
  - Attendre 2 secondes
  - Allumer la "Manette"
  - Sinon tout redémarrer
  - Sinon se référer au Dépannage de la section avancée
- Si la "Manette" se déconnecte fréquemment :
  - Redémarrer la "Manette"
  - Sinon changer/recharger la batterie
  - Sinon se référer au Dépannage de la section avancée

## Section avancée

### Prérequis

Extraire et installer ces logiciels

- PuTTY : https://the.earth.li/~sgtatham/putty/latest/w64/putty-64bit-0.78-installer.msi
- Pilotes CP210x : https://www.silabs.com/documents/public/software/CP210x_Universal_Windows_Driver.zip
- 7zip : https://www.7-zip.org
- InstalleurTD : https://github.com/Skkeye/TraceurDessinateur/releases/download/v0.1.0-alpha/InstalleurTD.zip

### Accéder à la console de commandes

- Ouvrez PuTTY
- Sélectionnez "Sériel" pour le type de connexion
- Entrez "115200" pour la Vitesse
- Pour trouver le port :
  - Naviguez dans InstalleurTD
  - Exécutez une première fois "Lister_Ports.bat"
  - Branchez le "Controlleur USB" dans l'ordinateur
  - Exécutez une seconde fois "Lister_Ports.bat"
  - Il devrait y avoir un port "COMx" de plus, c'est le port à choisir dans PuTTY
- Entrez le port trouve à l'étape 4 pour le port sériel
- Cliquez sur "Ouvrir"
- Entrez la commande "admin" suivie de la commande "help" pour voir si tout fonctionne

### Les commandes

- "help" : Affiche les commandes disponibles
- "log" : Affiche les messages envoyés par la "Manette"
- "nolog" : Annule la commande "log"
- "gyrozero" : Recalibre la "Manette" ; garder la "Manette" immobile durant ce processus
- "home" : Faire la mise à zéro de la position du "Dessinateur"
- "stop" : Désamorcer les moteurs du "Dessinateur"
- "start" : Réamorcer les moteurs du "Dessinateur" ; il est recommandé d'exécuter la commande "home" à la suite d'un réamorçage
- "pause" : Immobilise le "Dessinateur"
- "resume" : Annule la commande "pause"
- "restart" : Redémarre tout le système
- "admin" : Entre dans le mode administrateur de la console de commandes : le mode administrateur permet l'accès aux commandes
- "status" : Affiche l'état du serveur
- "exit" : Quitte le mode administrateur de la console de commandes

### Réinstaller les logiciels

#### Installer les pilotes

- Naviguez dans le dossier InstalleurTD
- Installez les Pilotes USB :
  - Prendre le "Contrôleur USB" et le brancher dans l'ordinateur en gardant le bouton blanc appuyé
  - Exécutez "Installer_Pilotes_Zadig.exe"
  - Cliquez le bouton "Install Drivers" et attendre que les pilotes soient installés
  - Fermer la fenêtre
- Naviguez dans le dossier CP210x_Universal_Windows_Driver
- Faites un clic droit sur "silabser.inf" et cliquez "Installer"

#### Installer le logiciel du "Contrôleur USB"

- Prendre le "Contrôleur USB" et le brancher dans l'ordinateur en gardant le bouton blanc appuyé
- Exécutez "Installer_Controleur.bat" et attendre que la fenêtre se referme
- Retirez le "Contrôleur USB" de l'ordinateur

#### Installer le logiciel du "Dessinateur"

- Prendre le "Dessinateur" et le brancher dans l'ordinateur en gardant le bouton blanc appuyé
- Exécutez "Installer_Dessinateur.bat" et attendre que la fenêtre se referme
- Retirez le "Dessinateur" de l'ordinateur

#### Installer le logiciel de la "Manette"

- Prendre la "Manette" et le brancher dans l'ordinateur en gardant le bouton étiqueté "Boot" appuyé
- Exécutez "Installer_Manette.bat", vous pouvez relâcher le bouton une fois connecte
- Une fois la fenêtre refermée, vous pouvez retirer la "Manette" de l'ordinateur

### Dépannage avancé

- Si les procédés de dépannage standard ne règlent pas le problème :
  - Utiliser la commende "status" pour savoir si tous les clients sont connectés
  - Si un client n'est pas connecté, éteindre et redémarrez la "Manette" et le "Dessinateur"
  - Sinon, utilisez la commande "restart" pour redémarrer le système complètement
  - Si aucune des méthodes ne règle le problème, réinstallez les logiciels

# Annexe C

## Manuel de dépannage

## Problème 1

Les mouvements de la machine CNC étaient saccadés et inconsistants.

### Tests

J’ai vérifié ce que le Serveur recevait en imprimant sur le port sériel les informations envoyées par la manette.

J’ai envoyé des informations à partir du serveur pour contrôler directement la machine CNC.

### Hypothèses

Le Dessinateur laissais tomber des instructions si elles arrivaient durant un déplacement

Le réseau MQTT était surcharge dû à la quantité de messages

### Meilleurs Tests

En imprimant directement les messages reçus sur le Dessinateur j’aurai pu voir exactement ce qu’il recevait.

### Modifications

J’ai changé la façon dont le dessinateur exécutait les instructions, en passant de traiter un déplacement lorsqu’une instruction était reçue à faire des déplacements de manière consistante et modifier les déplacements lorsqu’une instruction est reçue.

J’ai aussi réduit la fréquence à laquelle la Manette envoyait des messages pour alléger la demande sur le serveur MQTT.

### Vérification

J’ai utilisé la Manette pour contrôler le Dessinateur en repassant les tests effectués.

J’ai constaté que le mouvement était suffisamment stable pour les standards du projet.

## Problème 2

La remise à zéro de la position du Dessinateur ne fonctionnait pas.

### Tests

J’ai vérifié les connexions des moteurs aux contrôleurs et de ceux-ci au microcontrôleur.

J’ai aussi utilisé un oscilloscope pour voir si les signaux étaient bons et bien synchronisés.

J’ai finalement mis en marche la fonction de remise a zero, et j'ai manuellement appuyer sur les interrupteurs de limites.

### Hypothèses

La fonction chargée d’orchestrer les pas pour la mise à zéro n'active pas correctement les conditions de limites pour arrêter le moteur.

Les calculs de protections de limites de fin (distance maximale) avaient des conditions non fonctionnelles.

### Meilleurs Tests

Lire les commentaires laissés pour indiquer une fonctionnalité qui reste à implémenter.

### Modifications

Ajouter la fonctionnalité dans la fonction de remise à zéro pour déplacer les moteurs jusqu'à leurs interrupteurs de limites et de mettre à zéro leur positions par la suite.

### Vérification

Exécuter la fonction avec la machine CNC et si nécessaire refaire les tests effectués

## Problème 3

Un axe de la machine CNC était inversé.

### Tests

J’ai manuellement appuyer sur l’interrupteur de limite de l’axe inverse pour voir si ce n'était que durant la remise à zéro ou que c'était constant.

### Hypothèses

La direction par défaut n'était pas la bonne.

### Meilleurs Tests

Vérifier les connexions du dessinateur au contrôleur pour voir si le signal de direction se transmettait.

### Modifications

Reconnecter le fil du signal de direction correctement.

### Vérification

Mettre en marche le dessinateur et si nécessaire repasser les tests effectués.

## Liste des objectifs

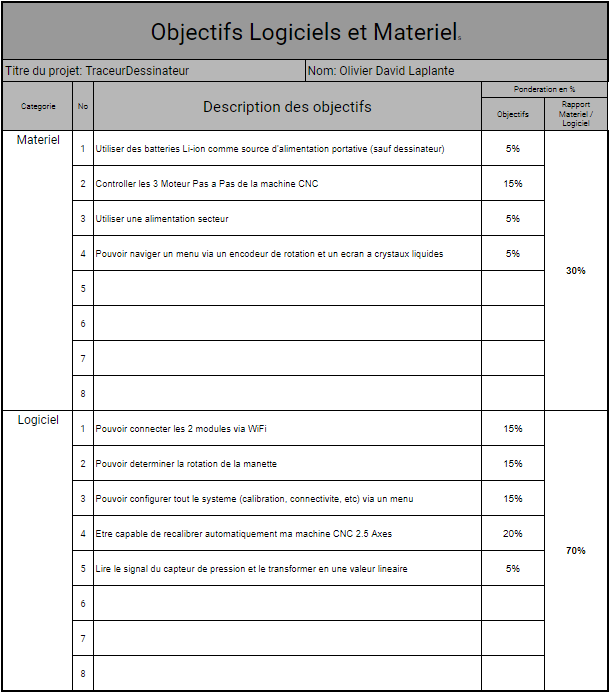
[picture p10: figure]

## Gantt

## Journal de Bord

Journal de bord : Projet d'intégration en TSO | | | | Jour de la semaine | Description du travail accompli durant la semaine | Prolèmes rencontrés | Solution au problème
Nom de l'étudiant: Olivier David Laplante
Semaine 1 | | | | Lundi | Recherche d'information sur les composants pour le plan initial | J'ai realise que je n'avais pas suffisamment de broches pour l'ecrant ACL | J'ai ajoute un 2e RPi Pico W en communication SPI avec le premier
| | | | Mardi | Recherche d'information sur les composants pour le plan initial
| | | | Mercredi | Recherche d'information sur les composants pour le plan initial
| | | | Jeudi | Recherche d'information sur les composants pour le plan initial | L'ecran TFT commande n'etait pas compatible avec les solutions de camera de mon projet | Acheter personnellement un ecrant HDMI pour la solution du Raspberry Pi
| | | | Vendredi | Recherche d'information sur les composants pour le plan initial Creation de la liste de pieces au magasin TGE | Le TEENSY41 avec la camera choisi n'ont pas un temps de rafraichissement assez vite pour mon application | Remplacer le TEENSY41 par un Raspberry Pi Pico W et la camera par une camera Raspberry Pi
Semaine 2 | | | | Lundi | Réalisation de la feuille de présentation
| | | | Mardi | Réalisation de la liste des objectifs
| | | | Mercredi | Réalisation de la liste des objectifs
| | | | Jeudi | Réalisation de l'échéancier
| | | | Vendredi | Réalisation de l'échéancier
Semaine 3 | | | | Lundi | Réalisation du Schématique du Contrôleur CNC Réalisation du Schématique de la Manette Réalisation du Schématique de la Caméra
| | | | Mardi | Réalisation du Schématique de la Manette Réalisation du Schématique de la Caméra Réalisation du Matriciel de la Caméra
| | | | Mercredi | Réalisation du Schématique de la Manette Réalisation du Schématique du CNC Réalisation du Matriciel de la Caméra Réalisation du Matriciel de la Manette
| | | | Jeudi
| | | | Vendredi
Semaine 4 | | | | Lundi | Réalisation du Schématique de la Manette Réalisation du Schématique de la Caméra Réalisation du Matriciel de la Manette Réalisation du Matriciel de la Caméra | Les connecteurs de Batteries n'etait pas les bons | J'ai change les footprints pour accommoder les nouveaux connecteurs
| | | | Mardi
| | | | Mercredi
| | | | Jeudi
| | | | Vendredi
Semaine 5 | | | | Lundi | Réalisation du Schématique du Contrôleur CNC Réalisation du Matriciel du Contrôleur CNC
| | | | Mardi | Réalisation du Matriciel du Contrôleur CNC | Les traces sur le Matriciel CNC n'etaient pas sur le bon cote | Mettre les traces sur le "BOTTOM"
| | | | Mercredi | Réalisation du schématique du Contrôleur CNC Réalisation du Matriciel du Contrôleur CNC Réalisation du Matriciel de la Caméra Réalisation du Matriciel de la Manette Perçage du PCB du CNC Perçage du PCB de la Caméra Perçage du PCB de la Manette | Les Matriciels n'etaient pas aux normes du departement TGE | Ajout de texte sur les Matriciels
| | | | Jeudi | Prendre connaissance de Doxygen pour documenter le code Soudage du PCB du CNC Soudage du PCB de la Manette Soudage du PCB de la Caméra
| | | | Vendredi | Installation de Doxygen Soudage du PCB du CNC Soudage du PCB de la Manette Soudage du PCB de la Caméra
Semaine 6 | | | | Lundi | Filage de la machine CNC | Le filage de la machine CNC n'etait pas clair ni assurement fonctionnel | Refaire completement le filage de la machine CNC
| | | | Mardi | Montage test du CNC Création du code prototype pour contrôler la machine CNC Test du CNC Développement de l'algorithme du déplacement linéaire pour CNC | J'ai un probleme ou la liste cree dans une fonction ne pourra pas etre retournee avec un pointeur | Passer un pointeur d'une liste deja cree dans les arguments pour modifier le contenu.
| | | | Mercredi | Développement de l'algorithme du déplacement linéaire pour CNC | L'algorithme ne produit pas les valeurs attendu et demande potentionellement trop de memoire | Refaire l'algorithme completement en python pour mieux le developper et le deverminer
| | | | Jeudi | Intégration de Doxygen au projet
| | | | Vendredi | Intégration de Doxygen au projet
Semaine 7 | | | | Lundi
| | | | Mardi
| | | | Mercredi
| | | | Jeudi
| | | | Vendredi
Semaine 8 | | | | Lundi
| | | | Mardi
| | | | Mercredi | | Le module de la camera etait trop ambitieux | Faire des modifications a la liste des objectifs avec mon superviseur de projet pour rendre le projet realisable dans le temps restant
| | | | Jeudi
| | | | Vendredi
Semaine 9 | | | | Lundi
| | | | Mardi
| | | | Mercredi
| | | | Jeudi
| | | | Vendredi
Semaine 10 | | | | Lundi
| | | | Mardi
| | | | Mercredi
| | | | Jeudi
| | | | Vendredi | Création initiale du module StepperWrapper Création du code test pour la manette
Semaine 11 | | | | Lundi | Documentation du code du module StepperWrapper
| | | | Mardi | Création du code final de la Manette
| | | | Mercredi | Déverminage du module StepperWrapper | Le code du module StepperWrapper ne fonctionnais pas / ne donnais pas de bonnes valeurs | Trouver la source du probleme (Implementation de l'algorithme de deplacement lineraire) et reparer le code errone
| | | | Jeudi | Création du code final du contrôleur Création du Serveur MQTT | La librairie de creation/lecture de packets ne fonctionne pas pour mon application | Transmettre tout via MQTT et la librairie "PubSubClient" en format json avec la librairie "ArduinoJson", ajouter un serveur Broker MQTT
| | | | Vendredi
Semaine 12 | | | | Lundi | Déverminage code Manette Ajout du menu dans une pseudo-console sur le Serveur MQTT | Les mise a jours d'informations venant de la manette n'etaient pas assez stable | Integrer FreeRTOS dans le code de la manette et ralentir la frequence d'envoie de mises a jour
| | | | Mardi | Test CNC Déverminage du code du CNC Déverminage du code de la manette | La mise a zero de la position du dessinateur bloquais ou ne marchais pas | Simplifier la methode de mise a zero en calibrant qu'un seul axe a la fois
| | | | Mercredi | Déverminage du code du CNC Déverminage du code de la manette | Les longueurs des axes du CNC était 4 fois trop court Les mises à jour de la manette étaient trop fréquentes Les déplacements étaient trop saccadés La mise à zéro des axes semblaient ne pas mettre à zéro les axes Les fonctions de protection de déplacement ne fonctionnaient qu'a moitie | Multiplier par 4 la longueur des axes et changer le type de variable Ralentir la fréquence d'envoi de mise à jour de la manette Se déplacer a une fréquence constante, modifier la vitesse sur une mise à jour Ajouter les lignes qui remettent à zéro les distances à la fonction de remise à zéro Retirer les fonctions de protection de déplacement
| | | | Jeudi
| | | | Vendredi

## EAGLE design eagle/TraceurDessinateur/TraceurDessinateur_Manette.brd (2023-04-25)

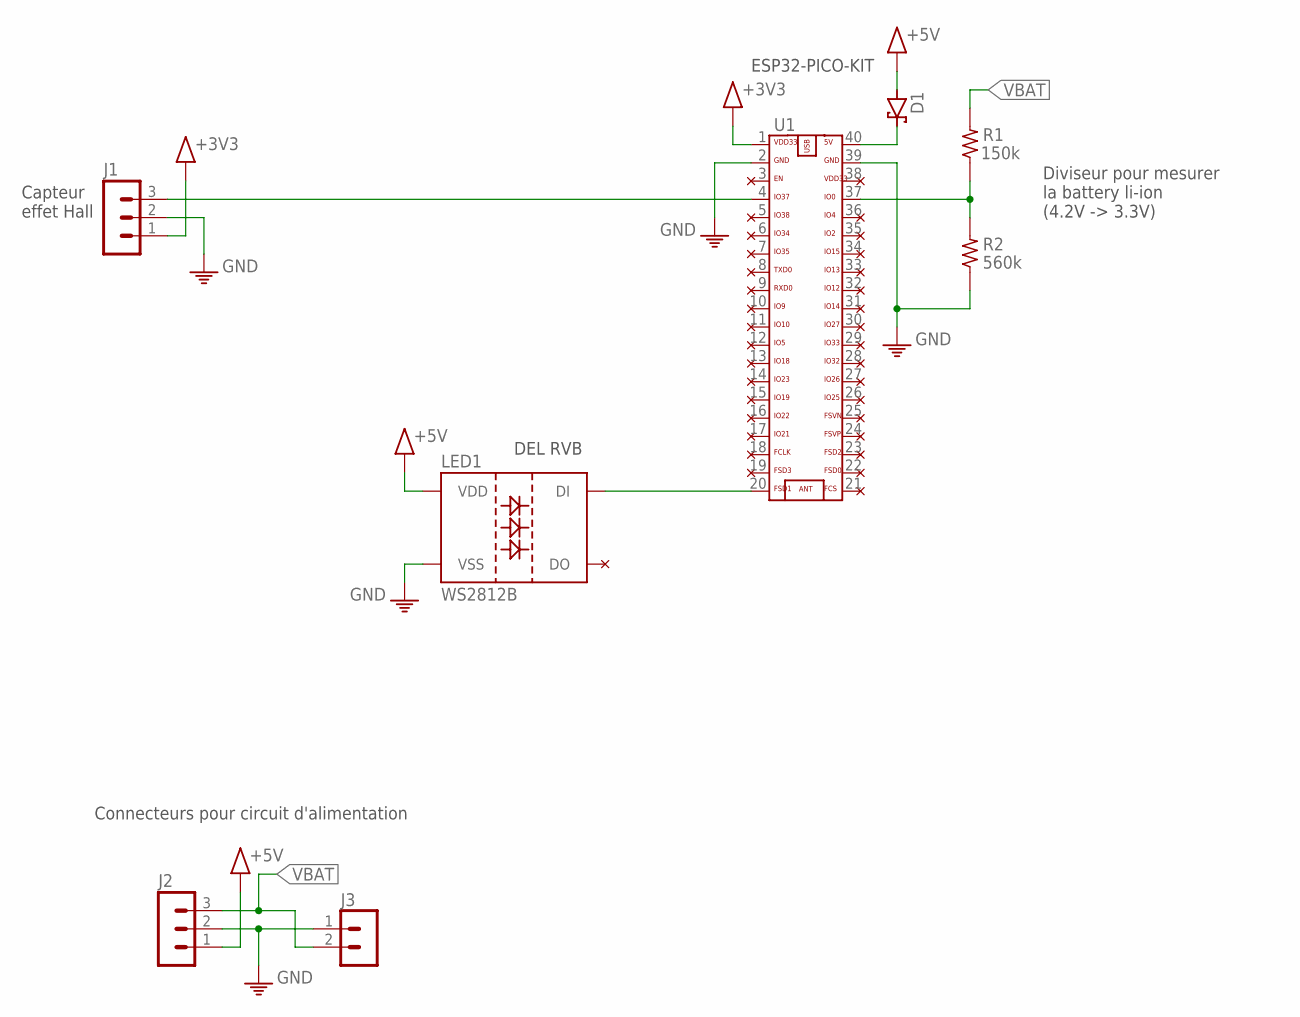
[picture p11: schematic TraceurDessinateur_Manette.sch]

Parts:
D1: 1N5817-B; DO41-7.6
J1, J2: MA03-1
J3: B2B-PH-K
LED1: WS2812B
R1: 150k; R1206W
R2: 560k; R1206W
U1: ESP32-PICO-V4-SOCKET

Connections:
+3V3: J1.1, U1.1 (3V3)
+5V: D1.A, J2.1, LED1.1 (VDD)
ADC_HALL: J1.3, U1.4
GND: J1.2, J2.2, J3.1, LED1.3 (VSS), R2.1, U1.2, U1.39
LED_DATA: LED1.4 (DI), U1.20
unnamed: D1.C, U1.40
VBAT: J2.3, J3.2, R1.2
VSENSE: R1.1, R2.2, U1.37

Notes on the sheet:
Capteur effet Hall
Connecteurs pour circuit d'alimentation
Diviseur pour mesurer la battery li-ion (4.2V -> 3.3V)
DEL RVB
ESP32-PICO-KIT

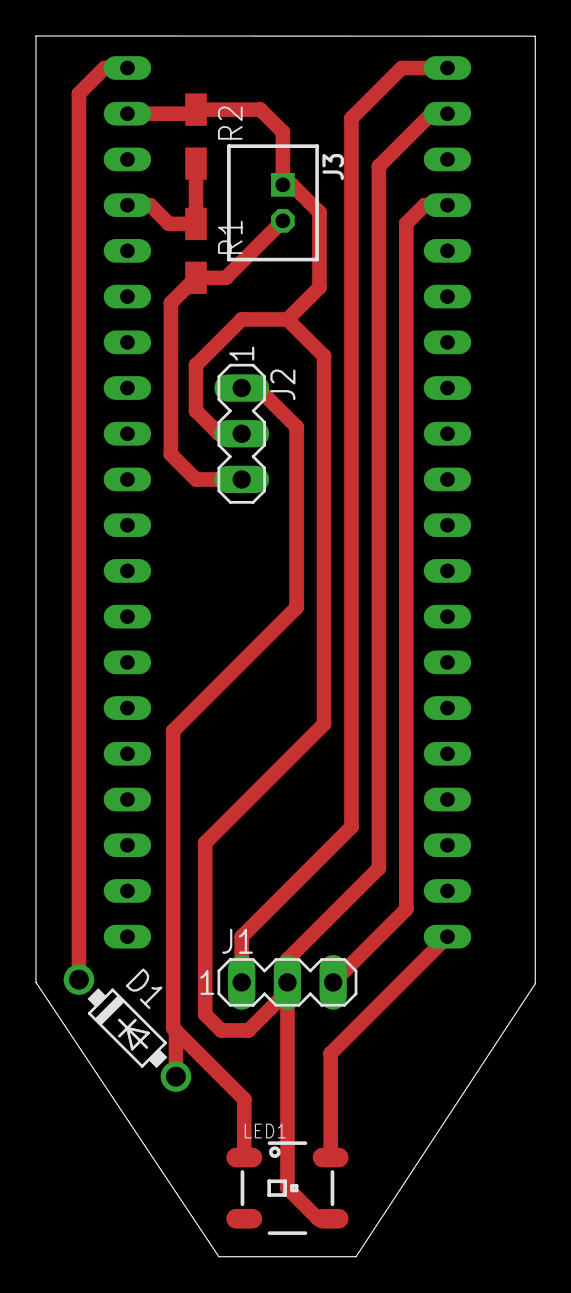
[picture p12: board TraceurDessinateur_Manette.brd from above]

Board: 2 copper layers, 27.7 x 67.8 mm, 9 parts (1 on the bottom side), 8 nets.

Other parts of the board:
U$35: A3L-LOC

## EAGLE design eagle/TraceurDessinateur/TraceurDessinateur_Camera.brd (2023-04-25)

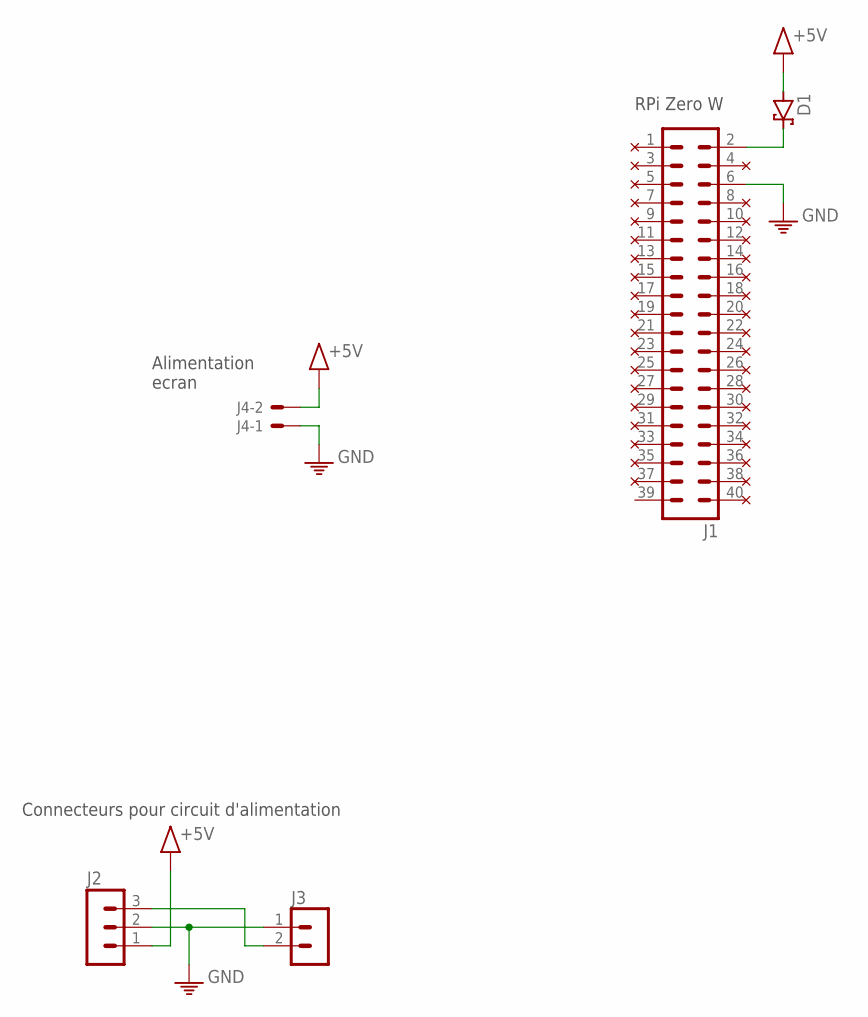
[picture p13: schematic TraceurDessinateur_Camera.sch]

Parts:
D1: 1N5817-B; DO41-7.6
J1: MA20-2
J2: MA03-1
J3: B2B-PH-K
J4: 22-23-2021

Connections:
+5V: D1.A, J2.1, J4.2
GND: J1.6, J2.2, J3.1, J4.1
unnamed: D1.C, J1.2
VBAT: J2.3, J3.2

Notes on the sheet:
RPi Zero W
Connecteurs pour circuit d'alimentation
Alimentation ecran

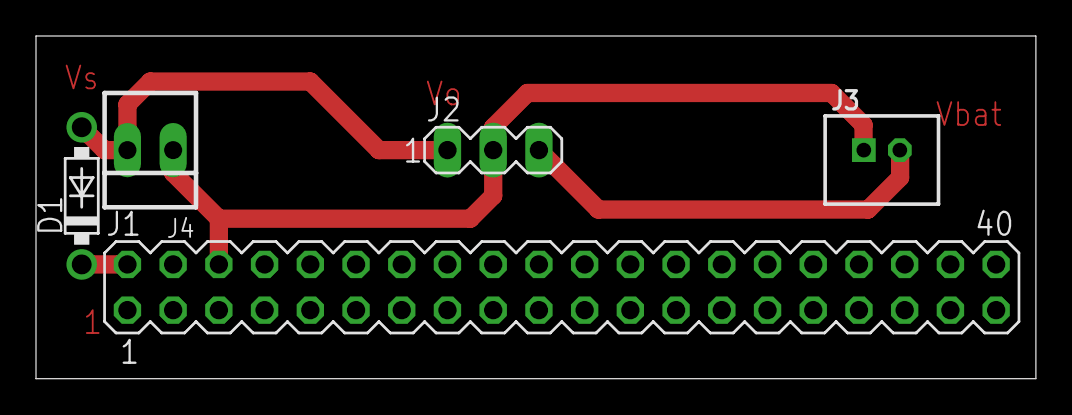
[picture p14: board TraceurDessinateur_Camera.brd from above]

Board: 2 copper layers, 55.5 x 19.0 mm, 6 parts (0 on the bottom side), 4 nets.

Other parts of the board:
U$37: A3L-LOC

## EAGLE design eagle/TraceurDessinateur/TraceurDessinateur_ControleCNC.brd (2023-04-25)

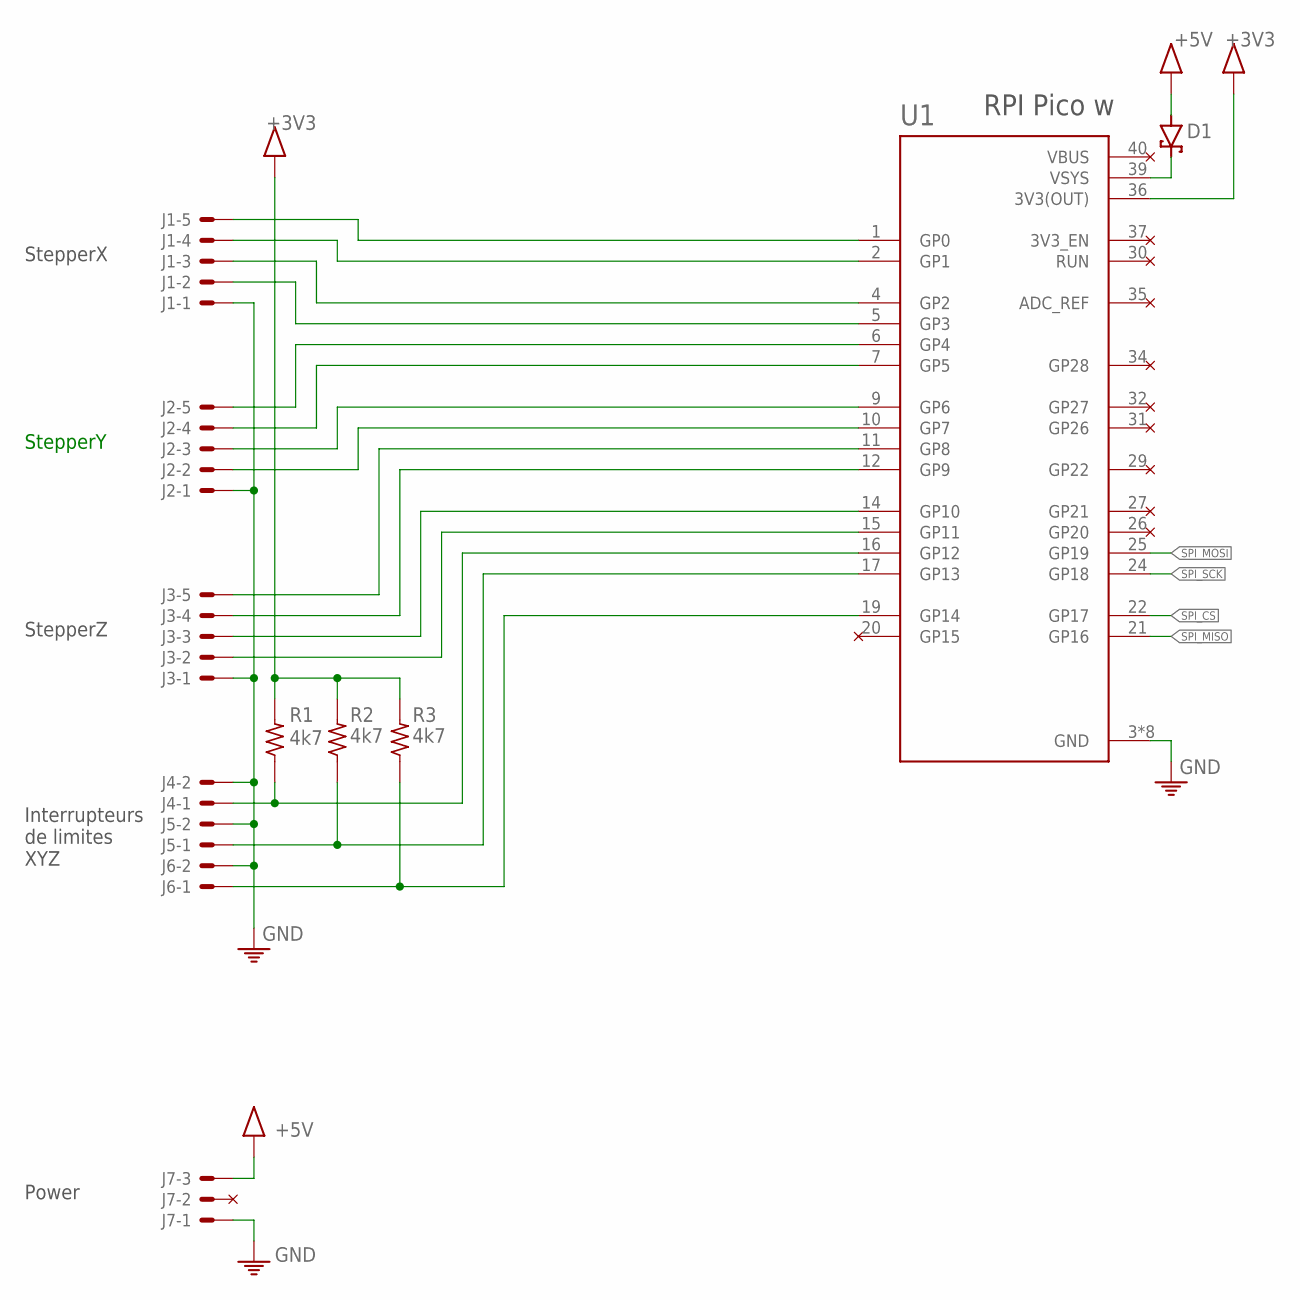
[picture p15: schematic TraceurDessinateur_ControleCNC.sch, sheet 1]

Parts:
D1: 1N5817-B; DO41-7.6
J1, J2, J3: 22-23-2051
J4, J5, J6: 22-23-2021
J7: 22-23-2031
R1, R2, R3: 4k7; R1206
U1: RASPBERRY_PICO-HEADERS-NO_DEBUGPICO-PKG-TH-NO_DEB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; PICO-PKG-TH-NO_DEBUG

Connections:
+3V3: R1.2, R2.2, R3.2, U1.36 (3V3(OUT)); also elsewhere on the board
+5V: D1.A, J7.3; also elsewhere on the board
GND: J1.1, J2.1, J3.1, J4.2, J5.2, J6.2, J7.1, U1.3 (GND), U1.8 (GND), U1.13 (GND), U1.18 (GND), U1.23 (GND), U1.28 (GND), U1.33 (GND), U1.38 (GND); also elsewhere on the board
unnamed: J1.5, U1.1 (GP0)
unnamed: J1.4, U1.2 (GP1)
unnamed: J1.3, U1.4 (GP2)
unnamed: J1.2, U1.5 (GP3)
unnamed: J2.5, U1.6 (GP4)
unnamed: J2.4, U1.7 (GP5)
unnamed: J2.3, U1.9 (GP6)
unnamed: J2.2, U1.10 (GP7)
unnamed: J3.5, U1.11 (GP8)
unnamed: J3.4, U1.12 (GP9)
unnamed: J3.3, U1.14 (GP10)
unnamed: J3.2, U1.15 (GP11)
unnamed: J4.1, R1.1, U1.16 (GP12)
unnamed: J5.1, R2.1, U1.17 (GP13)
unnamed: J6.1, R3.1, U1.19 (GP14)
unnamed: D1.C, U1.39 (VSYS)
SPI_CS: U1.22 (GP17); also elsewhere on the board
SPI_MISO: U1.21 (GP16); also elsewhere on the board
SPI_MOSI: U1.25 (GP19); also elsewhere on the board
SPI_SCK: U1.24 (GP18); also elsewhere on the board

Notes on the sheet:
StepperX
StepperY
StepperZ
Interrupteurs de limites XYZ
RPI Pico w
Power

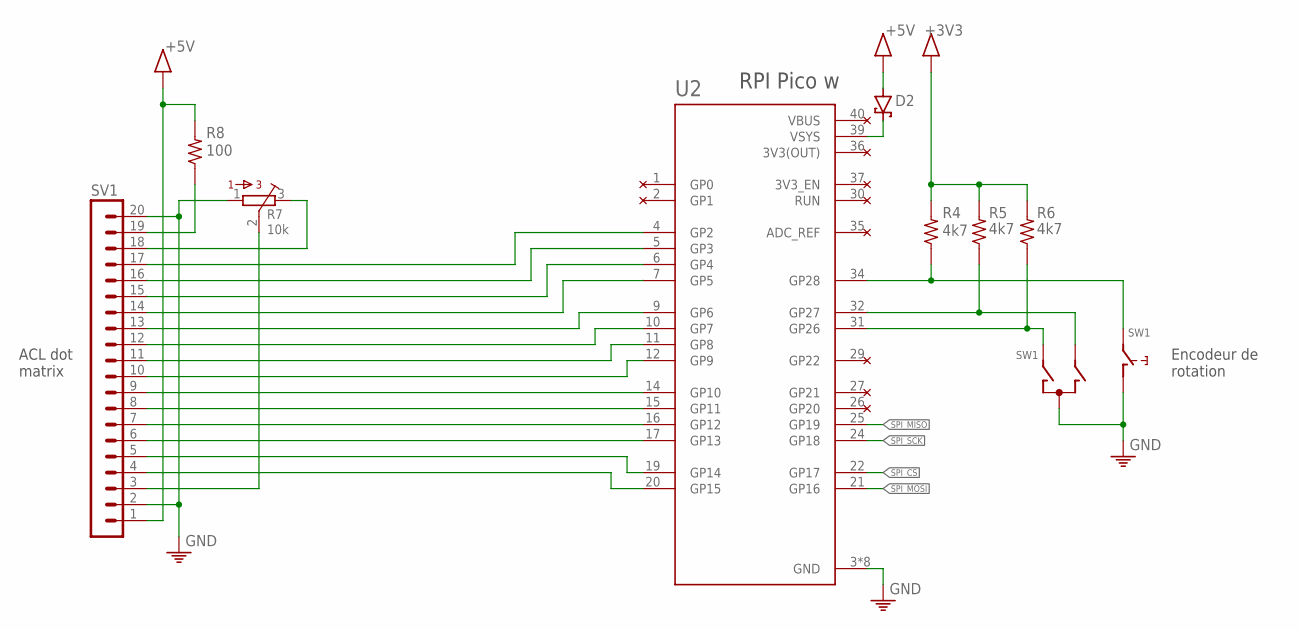
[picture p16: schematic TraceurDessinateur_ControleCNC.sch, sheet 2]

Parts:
D2: 1N5817-B; DO41-7.6
R4, R5, R6: 4k7; R1206
R7: 10k; 3362P
R8: 100; R1206
SV1: MA20-1
SW1: EC12E_SW; ALPS_EC12E_SW
U2: RASPBERRY_PICO-HEADERS-NO_DEBUGPICO-PKG-TH-NO_DEB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; PICO-PKG-TH-NO_DEBUG

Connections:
+3V3: R4.2, R5.2, R6.2; also elsewhere on the board
+5V: D2.A, R8.2, SV1.1; also elsewhere on the board
GND: U2.3 (GND), U2.8 (GND), U2.13 (GND), U2.18 (GND), U2.23 (GND), U2.28 (GND), U2.33 (GND), U2.38 (GND); also elsewhere on the board
unnamed: SV1.4, U2.20 (GP15)
unnamed: D2.C, U2.39 (VSYS)
unnamed: R6.1, SW1.A, U2.31 (GP26)
unnamed: R5.1, SW1.B, U2.32 (GP27)
unnamed: R4.1, SW1.E (2), U2.34 (GP28)
unnamed: SV1.5, U2.19 (GP14)
unnamed: SV1.6, U2.17 (GP13)
unnamed: SV1.7, U2.16 (GP12)
unnamed: SV1.8, U2.15 (GP11)
unnamed: SV1.9, U2.14 (GP10)
unnamed: SV1.10, U2.12 (GP9)
unnamed: SV1.11, U2.11 (GP8)
unnamed: SV1.12, U2.10 (GP7)
unnamed: SV1.13, U2.9 (GP6)
unnamed: SV1.14, U2.7 (GP5)
unnamed: SV1.15, U2.6 (GP4)
unnamed: SV1.16, U2.5 (GP3)
unnamed: SV1.17, U2.4 (GP2)
unnamed: R7.3, SV1.18
unnamed: R7.2, SV1.3
unnamed: R8.1, SV1.19
PE: R7.1, SV1.2, SV1.20, SW1.C, SW1.D (1)
SPI_CS: U2.22 (GP17); also elsewhere on the board
SPI_MISO: U2.25 (GP19); also elsewhere on the board
SPI_MOSI: U2.21 (GP16); also elsewhere on the board
SPI_SCK: U2.24 (GP18); also elsewhere on the board

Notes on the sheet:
ACL dot matrix
Encodeur de rotation
RPI Pico w

Board: 2 copper layers, 21 parts (0 on the bottom side), 45 nets, no tracks yet.

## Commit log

2023-01-23 Ajout de l'echeancier
2023-03-01 Python test code & code for CNC Steppers
2023-03-02 Cleanup et ajout de Doxygen
2023-04-13 fix: DessinStepper is good
    [DessinServos.ino, StepperWrapper.cpp]
2023-04-18 feat: command menu; fix: fast IMU updates
    [MQTTBroker.ino, Manette.ino]

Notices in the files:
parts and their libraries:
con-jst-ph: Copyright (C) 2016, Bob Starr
